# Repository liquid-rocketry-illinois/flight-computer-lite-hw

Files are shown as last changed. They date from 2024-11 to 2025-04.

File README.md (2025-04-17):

# Flight Computer Lite "Digital Tripper"
KiCad PCB repository for "Digital Tripper": a flight computer with no physical outputs designed for uncontrolled solid-fuel excursion flights (the first of which is planned for 2024-11), and a precursor for future flight computers that will incorporate actuation or active control or interact with other boards. The data it gathers will be used for verification of flight control and position estimation algorithms, flight vehicle design iteration, building up a strong avionics software backbone, and field-testing our electronic components and designs. Digital Tripper is a square 65mm on edge and fits transversely in a 4-inch-diameter model rocket.

<p align="center">
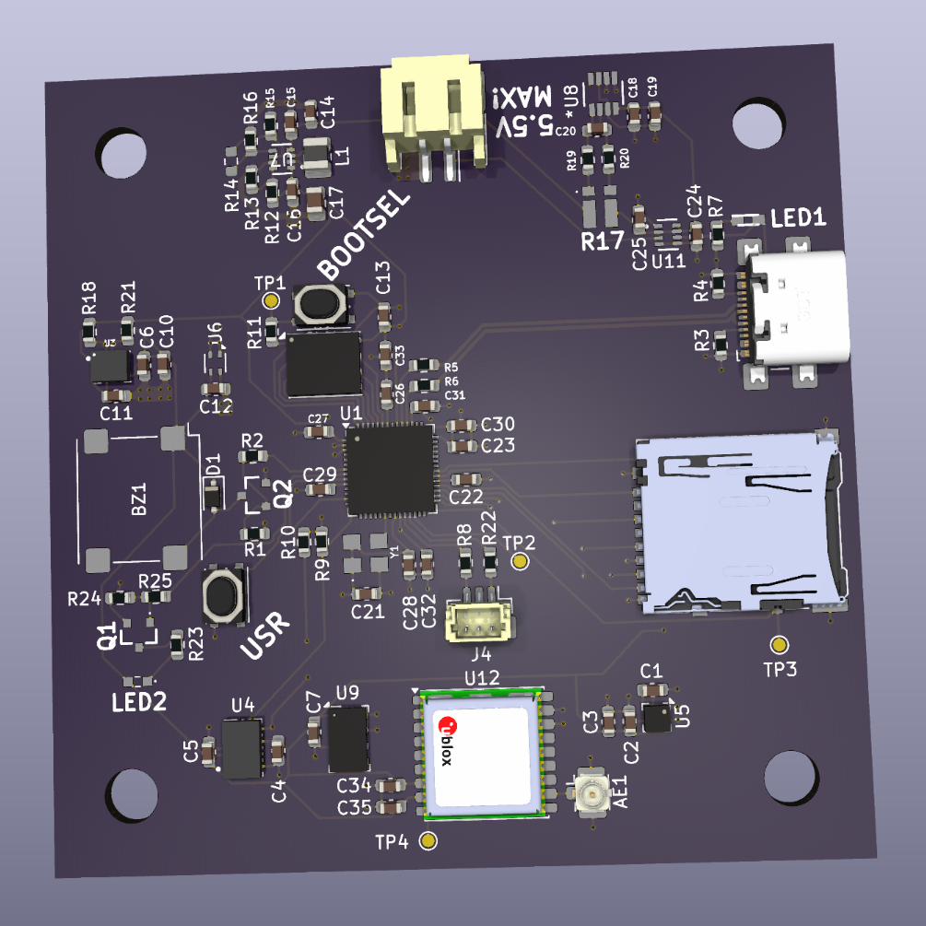
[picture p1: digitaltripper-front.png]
Digital Tripper front render
  
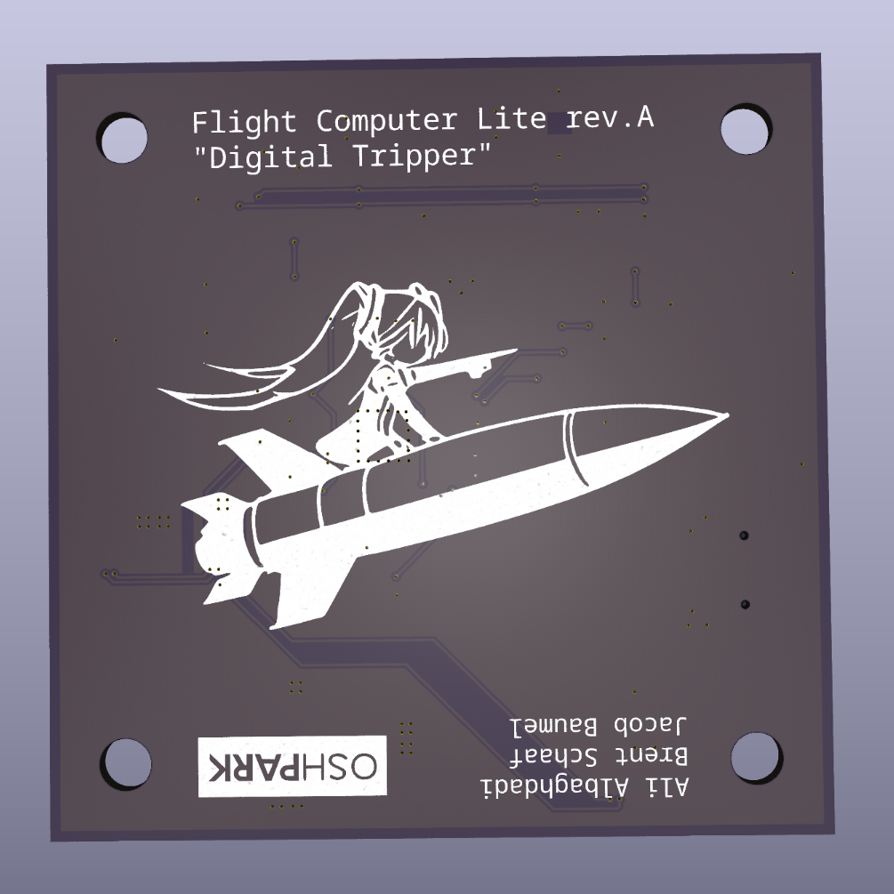
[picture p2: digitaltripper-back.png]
Digital Tripper back render
  
</p>

Ingredients:
* The "brain", a Raspberry Pi Silicon RP2040
* Various digital sensors
    * TDK InvenSense ICM-42688-P high-accuracy 6DoF IMU
    * Bosch BMI088 6DoF IMU for backup and a higher (24 g) acceleration limit
    * STmicroelectronics LIS3MDL 3-axis magnetometer
    * TE Connectivity MS5611 barometer/altimeter
    * Sensirion SHT40 for ambient temperature and humidity
    * u-blox MAX-M10S GNSS receiver with u.FL antenna
* A push-push microSD card slot for vibration-resistant datalogging
* A piezoelectric buzzer to provide audial status information before launch and after landing
* a USB-C port for programming and serial communication with the RP2040
* A JST-PH battery connector
* Power monitor IC to characterize necessary battery size
* A 3.3V-output switching DC-DC converter

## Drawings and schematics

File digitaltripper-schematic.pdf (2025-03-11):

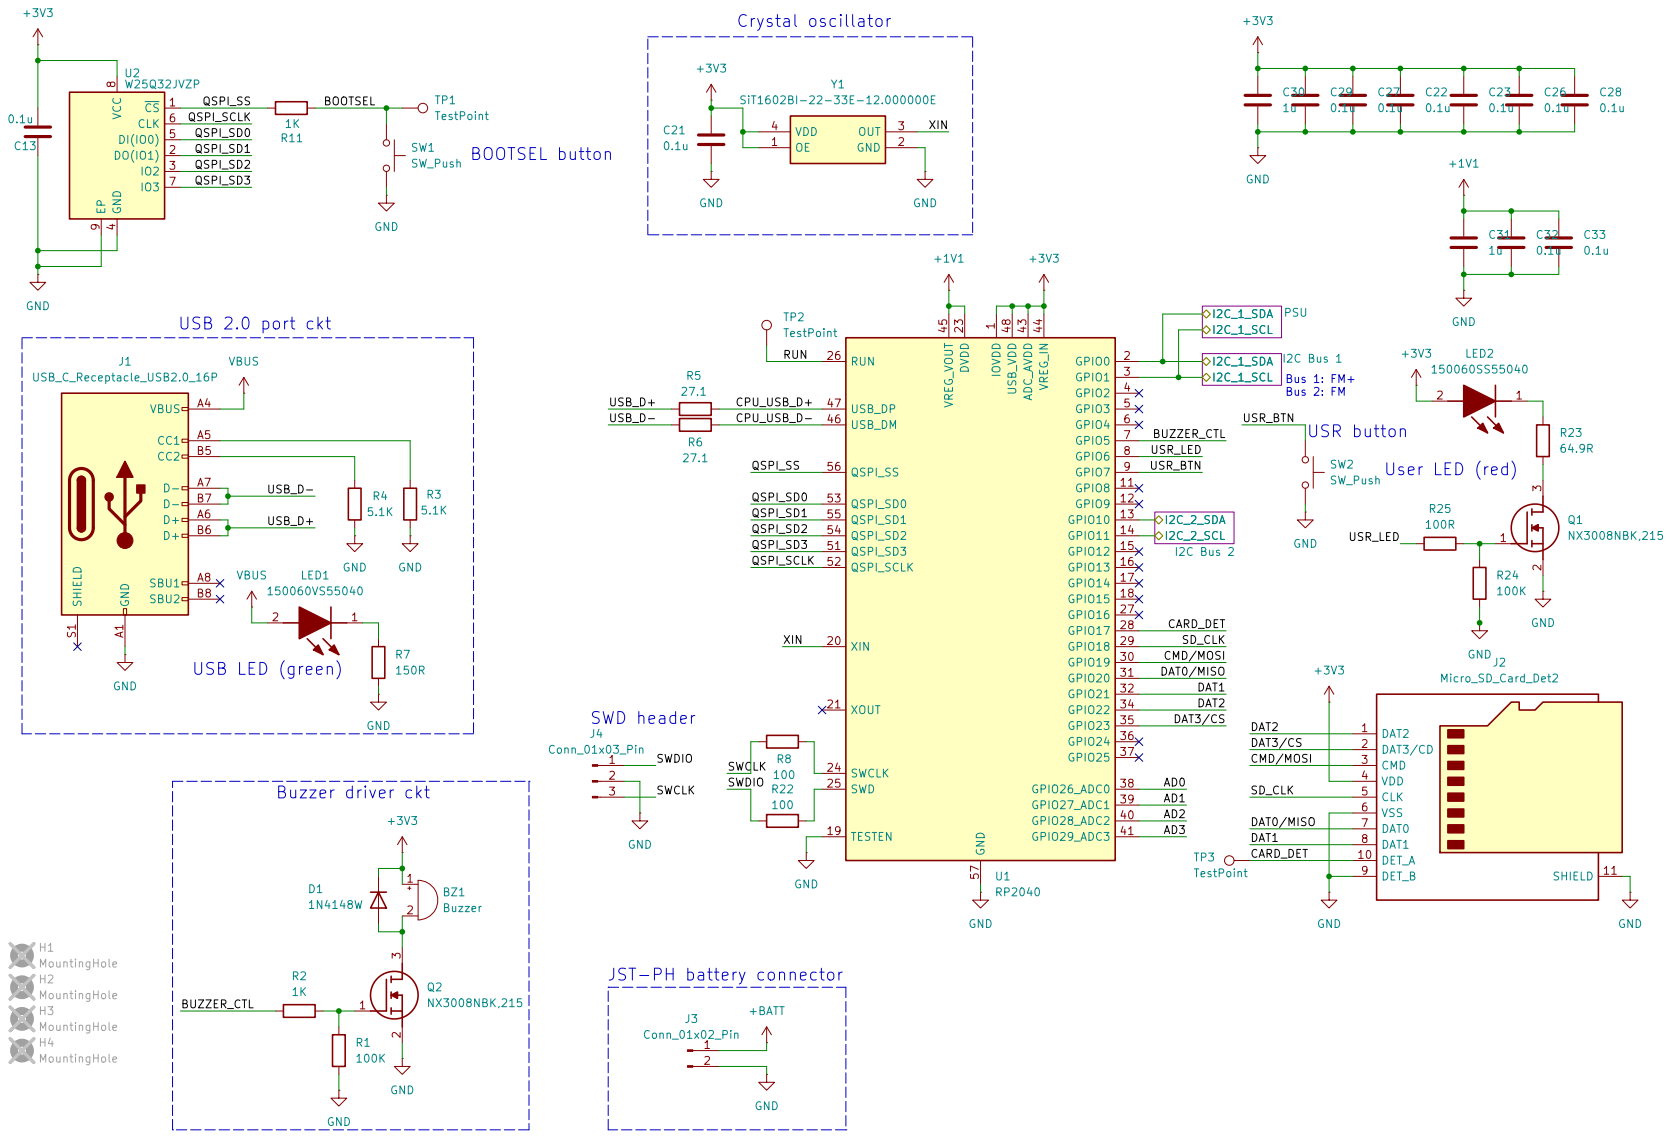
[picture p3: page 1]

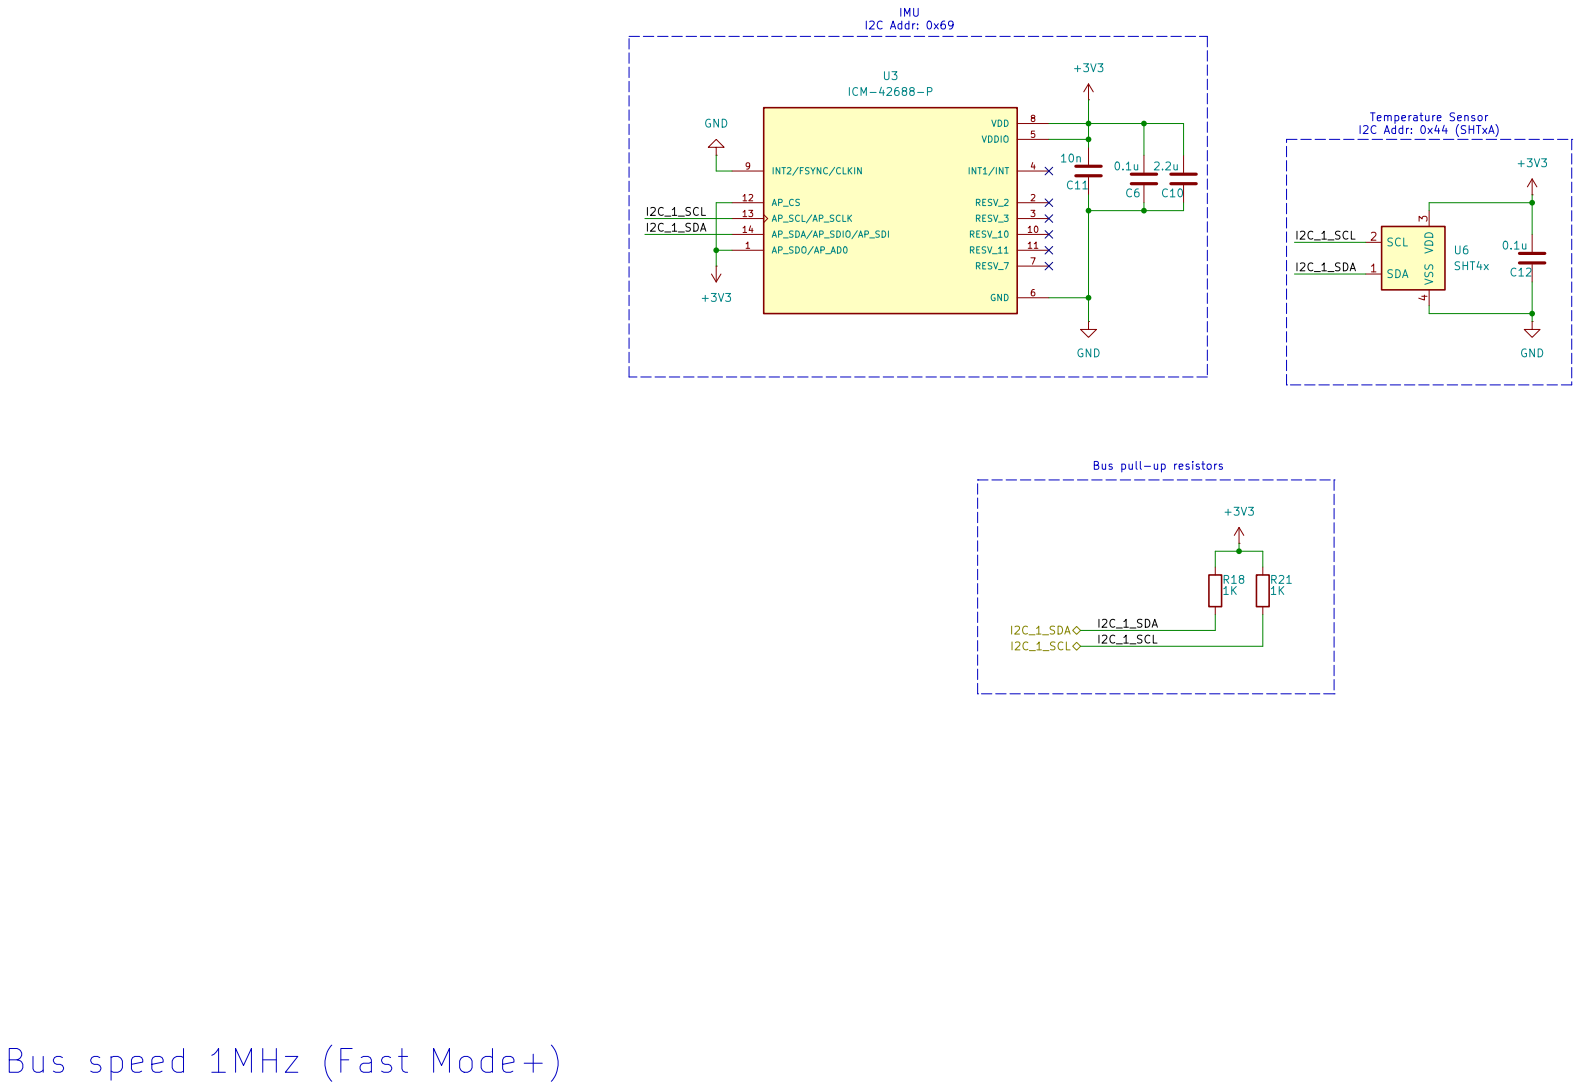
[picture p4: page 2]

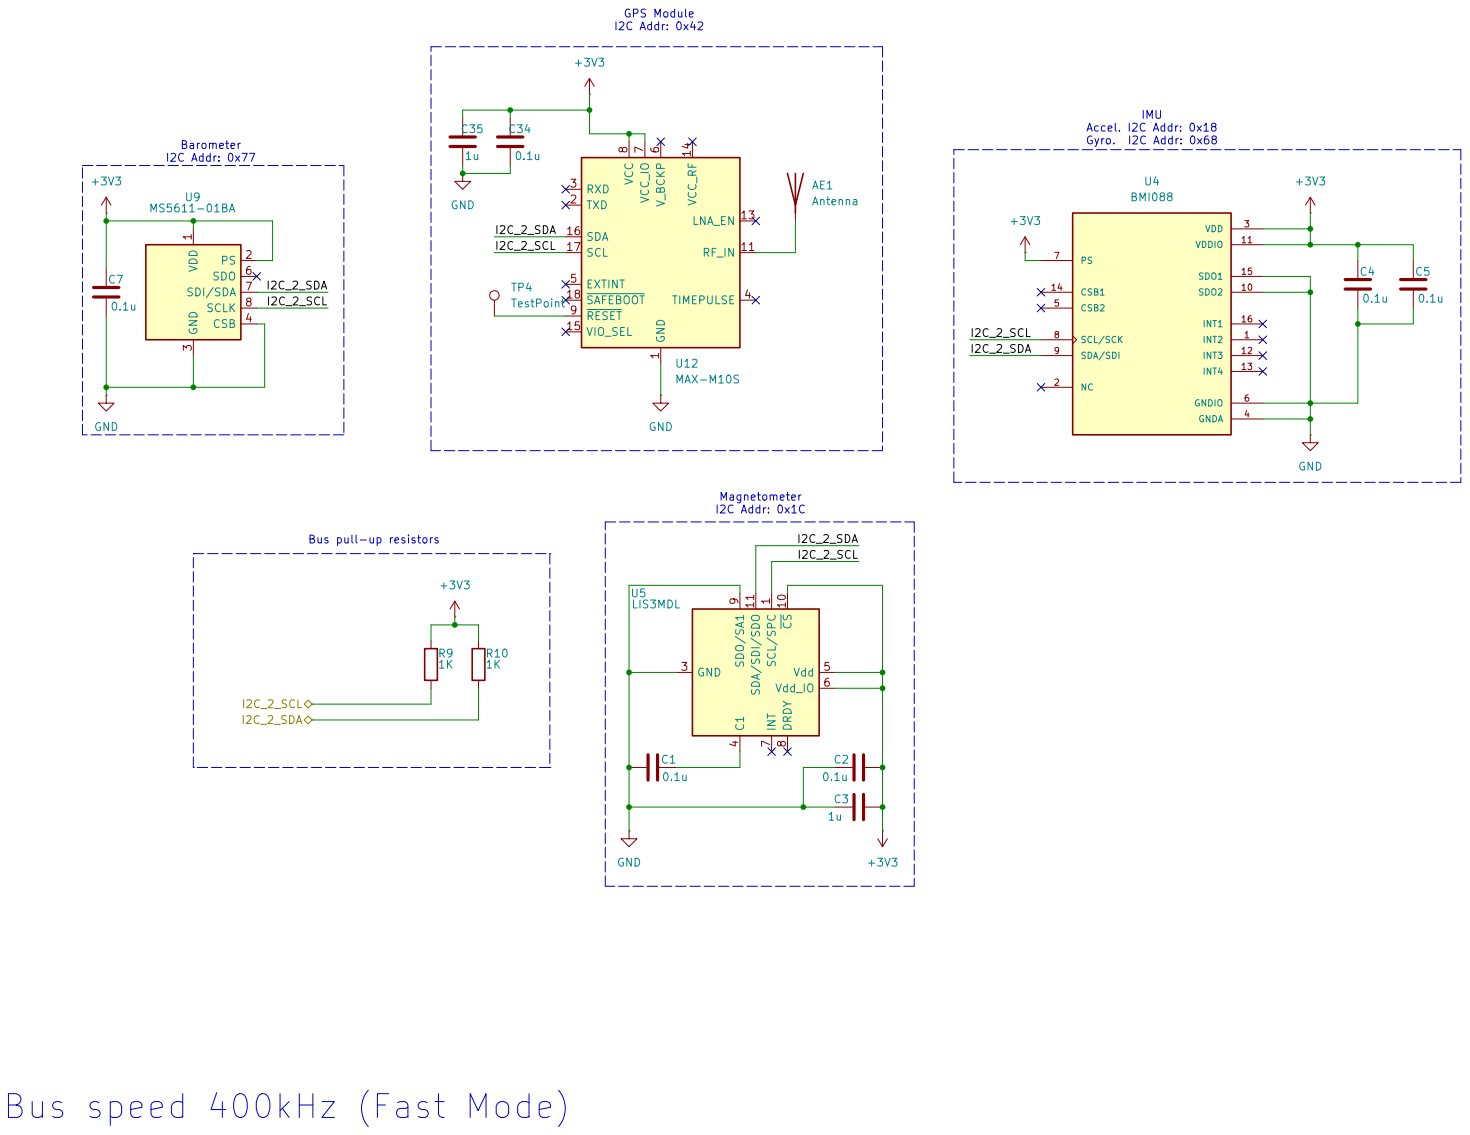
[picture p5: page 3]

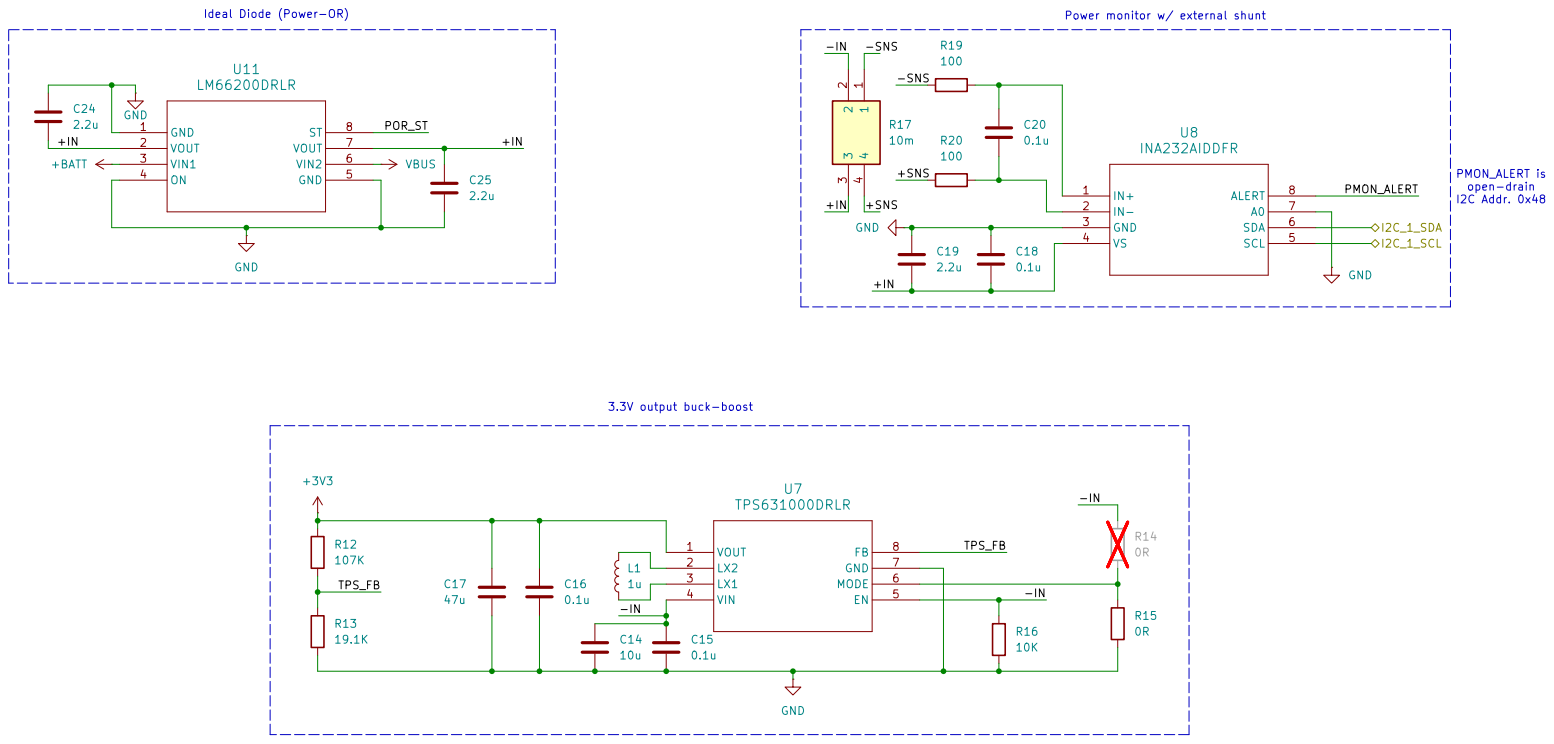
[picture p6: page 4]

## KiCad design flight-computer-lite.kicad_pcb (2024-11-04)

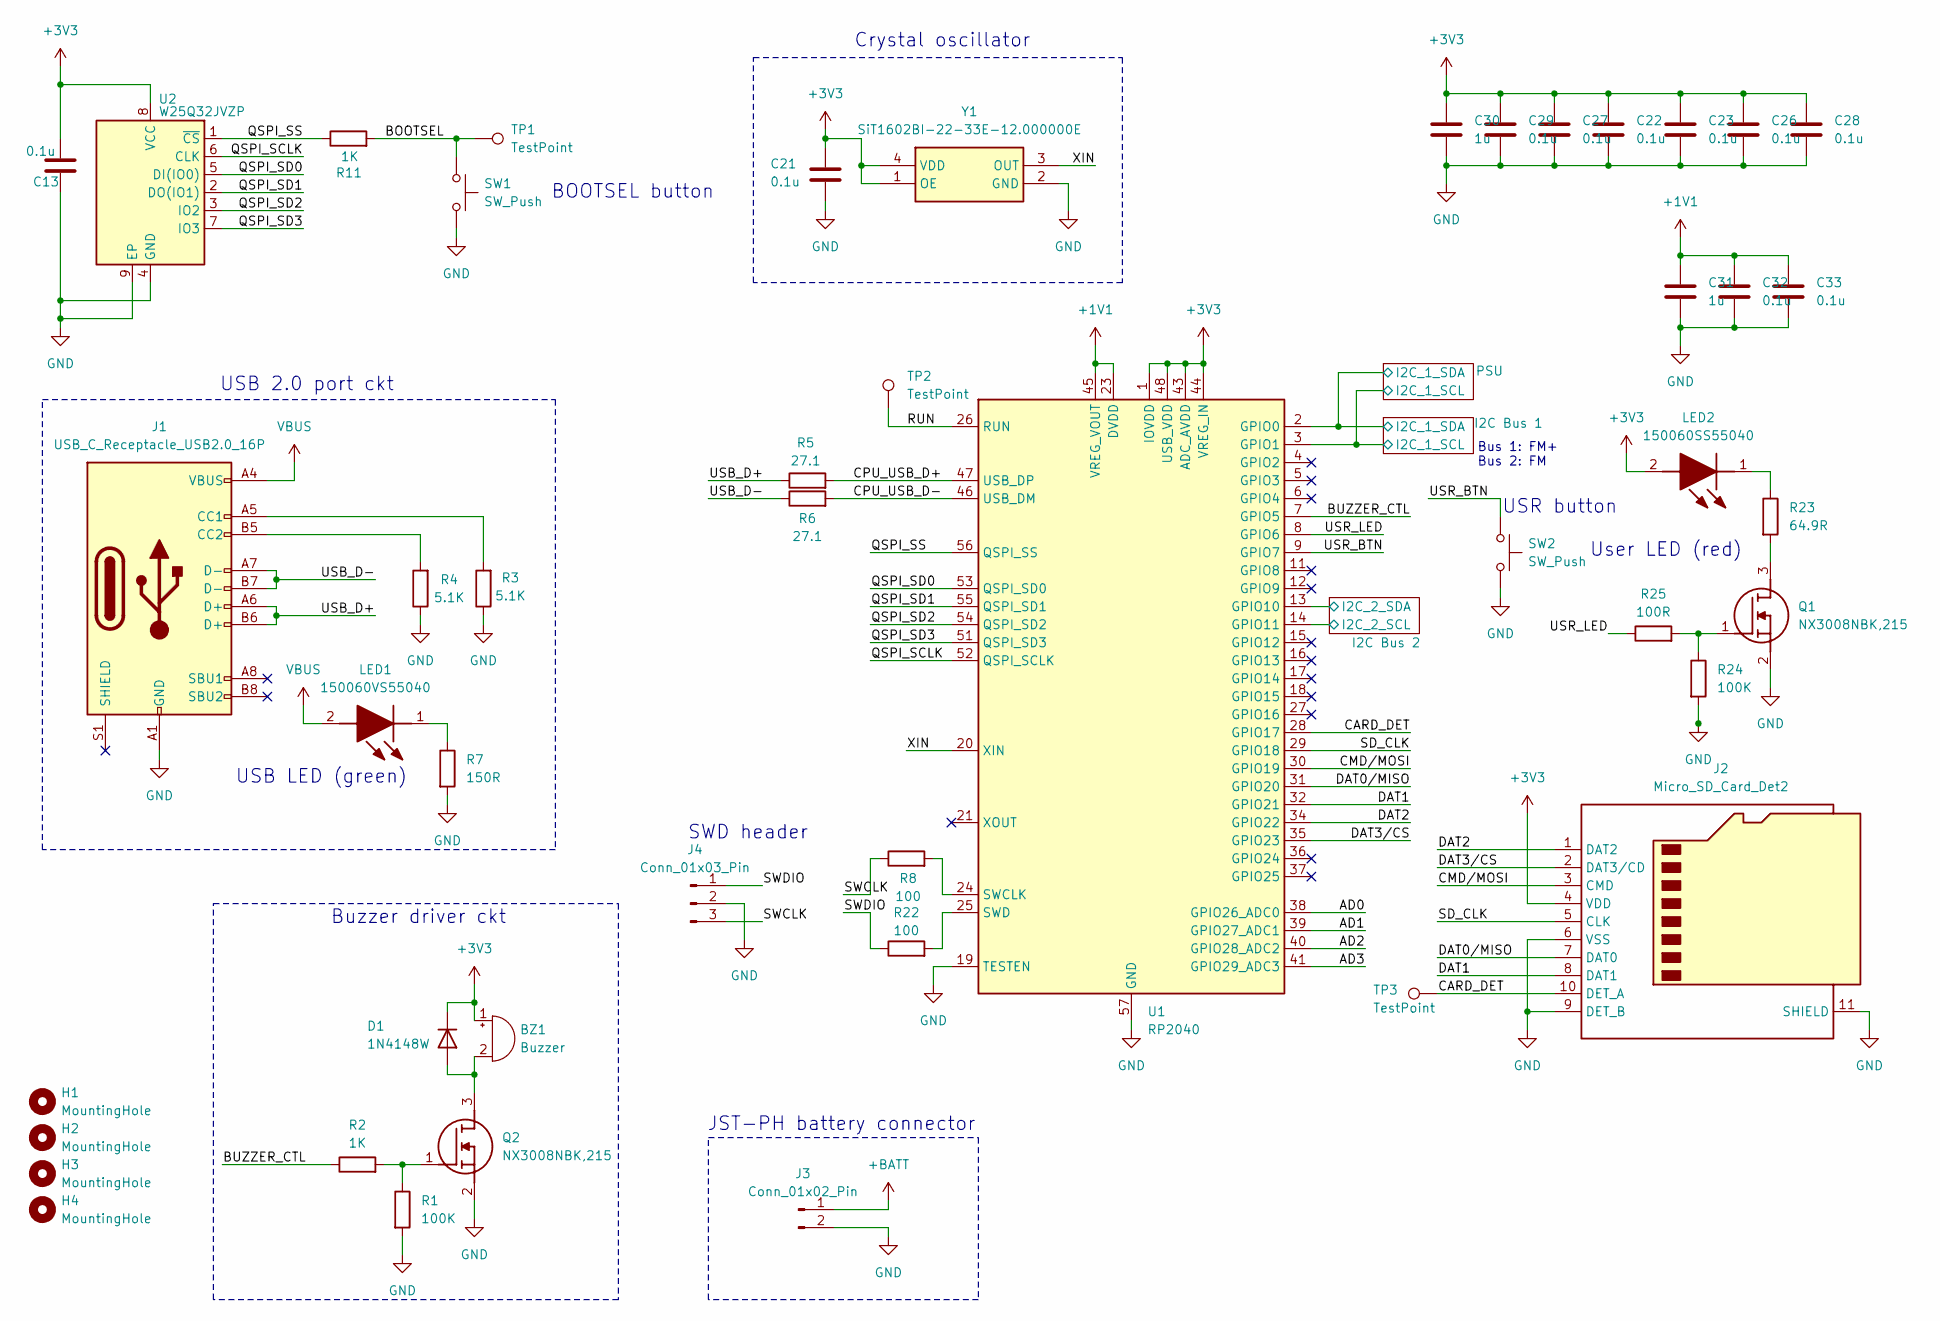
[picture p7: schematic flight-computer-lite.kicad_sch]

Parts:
BZ1: Buzzer; MagneticBuzzer_PUI_SMT-1028-T-2-R
C13, C21, C22, C23, C26, C27, C28, C29, C32, C33: 0.1u; C_0603_1608Metric
C30, C31: 1u; C_0603_1608Metric
D1: 1N4148W; D_SOD-323F
H1, H2, H3, H4: MountingHole; MountingHole_4.3mm_M4
J1: USB_C_Receptacle_USB2.0_16P; USB_C_Receptacle_GCT_USB4110
J2: Micro_SD_Card_Det2; microSD_HC_Hirose_DM3AT-SF-PEJM5
J3: Conn_01x02_Pin; JST_PH_S2B-PH-SM4-TB_1x02-1MP_P2.00mm_Horizontal
J4: Conn_01x03_Pin; JST_SH_BM03B-SRSS-TB_1x03-1MP_P1.00mm_Vertical
LED1: 150060VS55040; LEDM168X50N; Mouser Part Number 710-150060VS55040
LED2: 150060SS55040; Mouser Part Number 710-150060SS55040
Q1, Q2: NX3008NBK,215; NX3008NBK215; Mouser Part Number 771-NX3008NBK,215
R1, R24: 100K; R_0603_1608Metric
R2, R11: 1K; R_0603_1608Metric
R3, R4: 5.1K; R_0603_1608Metric
R5, R6: 27.1; R_0603_1608Metric
R7: 150R; R_0603_1608Metric
R8, R22: 100; R_0603_1608Metric
R23: 64.9R; R_0603_1608Metric
R25: 100R; R_0603_1608Metric
SW1, SW2: SW_Push; SW_Push_1P1T_NO_Vertical_Wuerth_434133025816
TP1, TP2, TP3: TestPoint; TestPoint_Pad_D1.0mm
U1: RP2040; QFN-56-1EP_7x7mm_P0.4mm_EP3.2x3.2mm
U2: W25Q32JVZP; WSON-8-1EP_6x5mm_P1.27mm_EP3.4x4.3mm
Y1: SiT1602BI-22-33E-12.000000E; SIT1602BI2233E12000000G; Manufacturer_Part_Number SiT1602BI-22-33E-12.000000E; Mouser Part Number N/A

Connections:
+1V1: C31.1, C32.1, C33.1, U1.23 (DVDD), U1.45 (VREG_VOUT), U1.50 (DVDD)
+3V3: BZ1.1 (+), C13.1, C21.1, C22.1, C23.1, C26.1, C27.1, C28.1, C29.1, C30.1, D1.1 (K), J2.4 (VDD), LED2.2 (A), U1.1 (IOVDD), U1.10 (IOVDD), U1.22 (IOVDD), U1.33 (IOVDD), U1.42 (IOVDD), U1.43 (ADC_AVDD), U1.44 (VREG_IN), U1.48 (USB_VDD), U1.49 (IOVDD), U2.8 (VCC), Y1.1 (OE), Y1.4 (VDD); also elsewhere on the board
+BATT: J3.1; also elsewhere on the board
/AD0: U1.38 (GPIO26_ADC0)
/AD1: U1.39 (GPIO27_ADC1)
/AD2: U1.40 (GPIO28_ADC2)
/AD3: U1.41 (GPIO29_ADC3)
/BOOTSEL: R11.2, SW1.1, TP1.1
/BUZZER_CTL: R2.1, U1.7 (GPIO5)
/CARD_DET: J2.10 (DET_A), TP3.1, U1.28 (GPIO17)
/CMD/MOSI: J2.3 (CMD), U1.30 (GPIO19)
/CPU_USB_D+: R5.2, U1.47 (USB_DP)
/CPU_USB_D-: R6.2, U1.46 (USB_DM)
/DAT0/MISO: J2.7 (DAT0), U1.31 (GPIO20)
/DAT1: J2.8 (DAT1), U1.32 (GPIO21)
/DAT2: J2.1 (DAT2), U1.34 (GPIO22)
/DAT3/CS: J2.2 (DAT3/CD), U1.35 (GPIO23)
/I2C Bus 1/I2C_1_SCL: U1.3 (GPIO1); also elsewhere on the board
/I2C Bus 1/I2C_1_SDA: U1.2 (GPIO0); also elsewhere on the board
/I2C Bus 2/I2C_2_SCL: U1.14 (GPIO11); also elsewhere on the board
/I2C Bus 2/I2C_2_SDA: U1.13 (GPIO10); also elsewhere on the board
/QSPI_SCLK: U1.52 (QSPI_SCLK), U2.6 (CLK)
/QSPI_SD0: U1.53 (QSPI_SD0), U2.5 (DI(IO0))
/QSPI_SD1: U1.55 (QSPI_SD1), U2.2 (DO(IO1))
/QSPI_SD2: U1.54 (QSPI_SD2), U2.3 (IO2)
/QSPI_SD3: U1.51 (QSPI_SD3), U2.7 (IO3)
/QSPI_SS: R11.1, U1.56 (QSPI_SS), U2.1 (~CS)
/RUN: TP2.1, U1.26 (RUN)
/SD_CLK: J2.5 (CLK), U1.29 (GPIO18)
/SWCLK: J4.3, R8.1
/SWDIO: J4.1, R22.1
/USB_D+: J1.A6 (D+), J1.B6 (D+), R5.1
/USB_D-: J1.A7 (D-), J1.B7 (D-), R6.1
/USR_BTN: SW2.1, U1.9 (GPIO7)
/USR_LED: R25.1, U1.8 (GPIO6)
/XIN: U1.20 (XIN), Y1.3 (OUT)
GND: C13.2, C21.2, C22.2, C23.2, C26.2, C27.2, C28.2, C29.2, C30.2, C31.2, C32.2, C33.2, J1.A1 (GND), J1.A12 (GND), J1.B1 (GND), J1.B12 (GND), J2.6 (VSS), J2.9 (DET_B), J2.11 (SHIELD), J3.2, J4.2, J4.MP, Q1.2 (S), Q2.2 (S), R1.2, R3.1, R4.1, R7.2, R24.2, SW1.2, SW2.2, U1.19 (TESTEN), U1.57 (GND), U2.4 (GND), U2.9 (EP), Y1.2 (GND); also elsewhere on the board
unnamed: BZ1.2 (-), D1.2 (A), Q2.3 (D)
unnamed: J1.A5 (CC1), R3.2
unnamed: J1.B5 (CC2), R4.2
unnamed: LED1.1 (K), R7.1
unnamed: LED2.1 (K), R23.1
unnamed: Q1.3 (D), R23.2
unnamed: Q1.1 (G), R24.1, R25.2
unnamed: Q2.1 (G), R1.1, R2.2
unnamed: R8.2, U1.24 (SWCLK)
unnamed: R22.2, U1.25 (SWD)
VBUS: J1.A4 (VBUS), J1.A9 (VBUS), J1.B4 (VBUS), J1.B9 (VBUS), LED1.2 (A); also elsewhere on the board

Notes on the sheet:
Bus 1: FM+ Bus 2: FM
Buzzer driver ckt
JST-PH battery connector
BOOTSEL button
User LED (red)
SWD header
USB LED (green)
USR button
Crystal oscillator
USB 2.0 port ckt

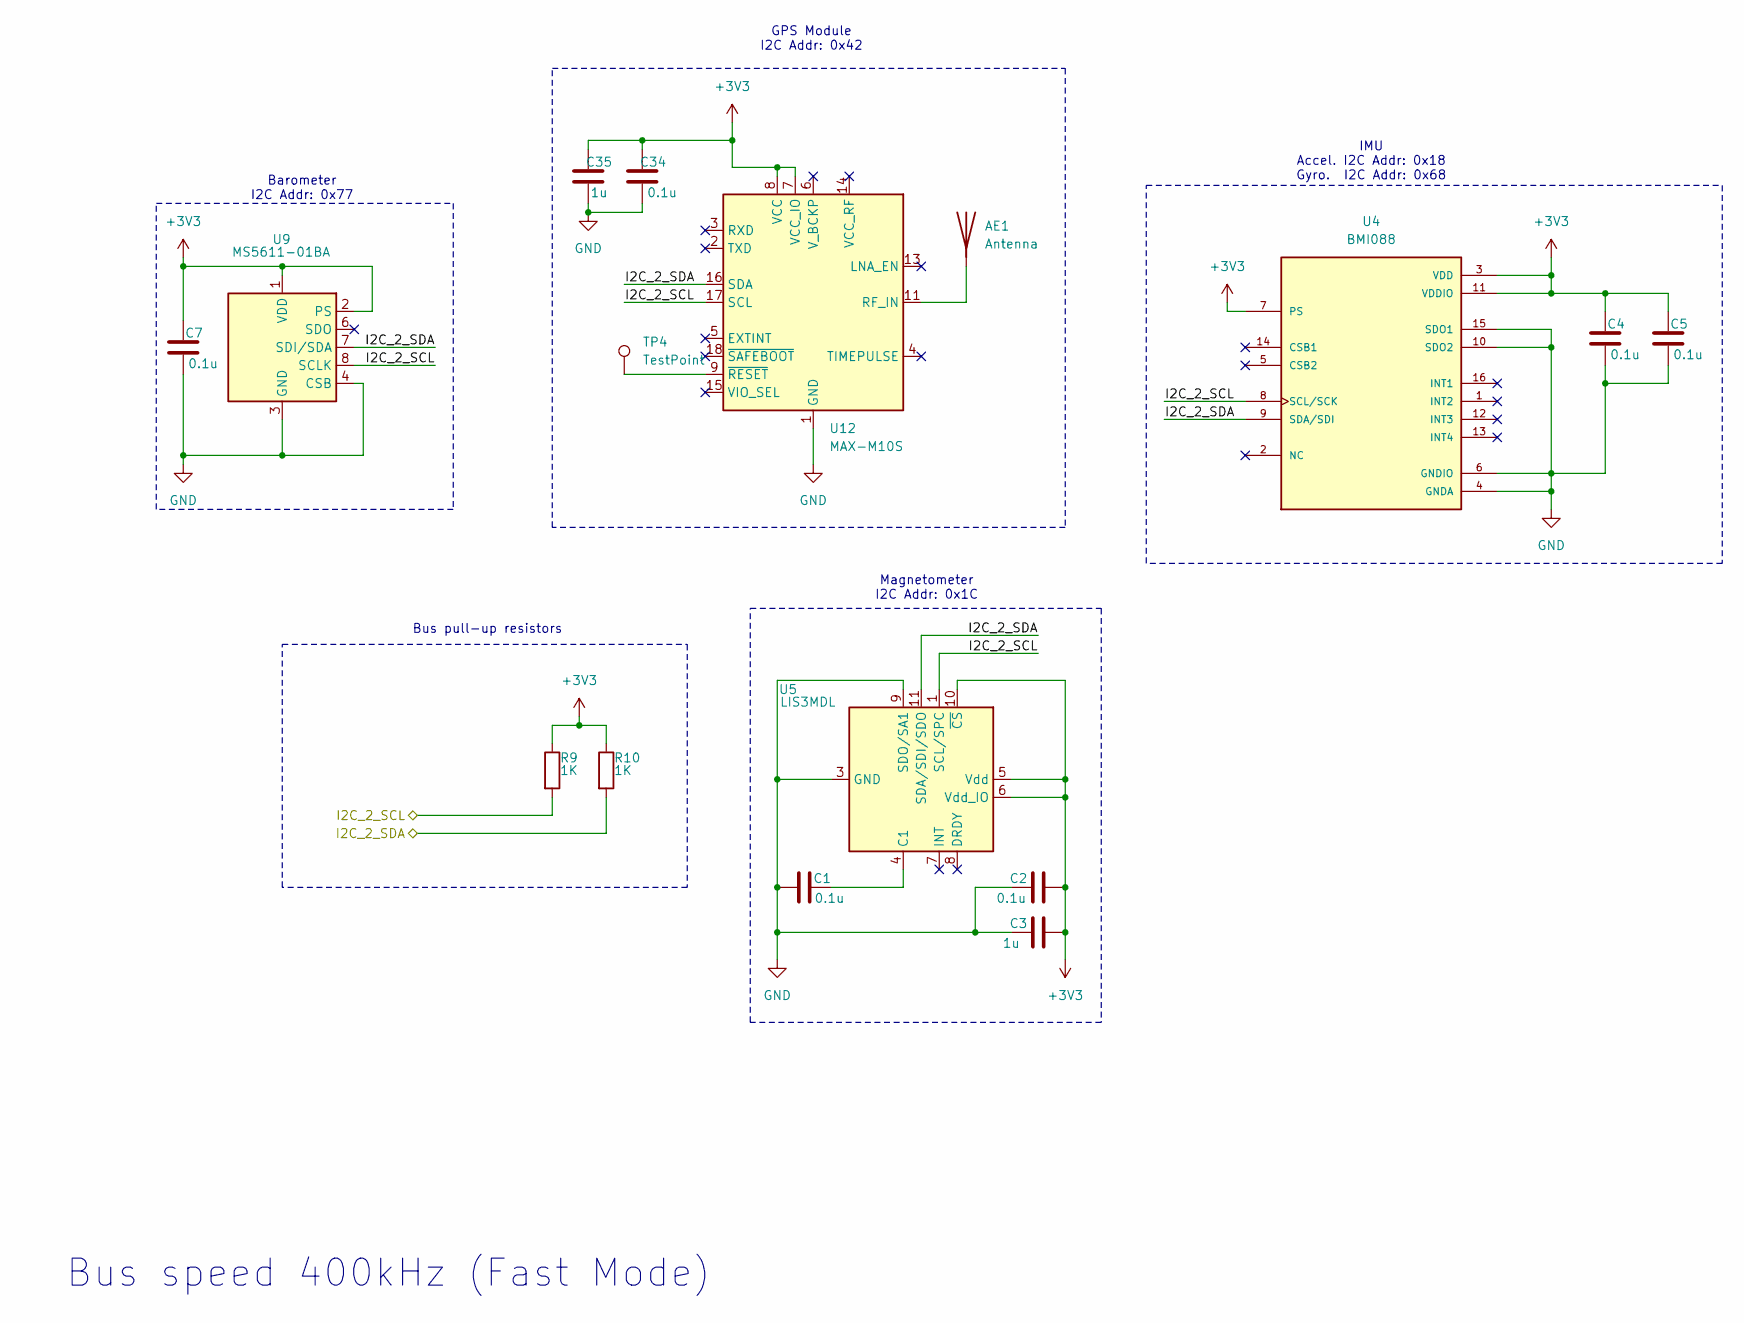
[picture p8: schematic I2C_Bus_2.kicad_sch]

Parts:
AE1: Antenna; U.FL_Hirose_U.FL-R-SMT-1_Vertical
C1, C2, C4, C5, C7, C34: 0.1u; C_0603_1608Metric
C3, C35: 1u; C_0603_1608Metric
R9, R10: 1K; R_0603_1608Metric
TP4: TestPoint; TestPoint_Pad_D1.0mm
U4: BMI088; PQFN50P450X300X100-16N
U5: LIS3MDL; LGA-12_2x2mm_P0.5mm
U9: MS5611-01BA; LGA-8_3x5mm_P1.25mm
U12: MAX-M10S; ublox_MAX

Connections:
+3V3: C2.2, C3.2, C4.2, C5.2, C7.2, C34.2, C35.2, R9.1, R10.1, U4.3 (VDD), U4.7 (PS), U4.11 (VDDIO), U5.5 (Vdd), U5.6 (Vdd_IO), U5.10 (~CS), U9.1 (VDD), U9.2 (PS), U12.7 (VCC_IO), U12.8 (VCC); also elsewhere on the board
/I2C Bus 2/I2C_2_SCL: R9.2, U4.8 (SCL/SCK), U5.1 (SCL/SPC), U9.8 (SCLK), U12.17 (SCL); also elsewhere on the board
/I2C Bus 2/I2C_2_SDA: R10.2, U4.9 (SDA/SDI), U5.11 (SDA/SDI/SDO), U9.7 (SDI/SDA), U12.16 (SDA); also elsewhere on the board
GND: AE1.2, C1.1, C2.1, C3.1, C4.1, C5.1, C7.1, C34.1, C35.1, U4.4 (GNDA), U4.6 (GNDIO), U4.10 (SDO2), U4.15 (SDO1), U5.2 (GND), U5.3 (GND), U5.9 (SDO/SA1), U5.12 (GND), U9.3 (GND), U9.4 (CSB), U9.5 (CSB), U12.1 (GND), U12.10 (GND), U12.12 (GND); also elsewhere on the board
unnamed: AE1.1 (A), U12.11 (RF_IN)
unnamed: C1.2, U5.4 (C1)
unnamed: TP4.1, U12.9 (~RESET)

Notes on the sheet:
Magnetometer I2C Addr: 0x1C
IMU Accel. I2C Addr: 0x18 Gyro. I2C Addr: 0x68
GPS Module I2C Addr: 0x42
Bus pull-up resistors
Bus speed 400kHz (Fast Mode)
Barometer I2C Addr: 0x77

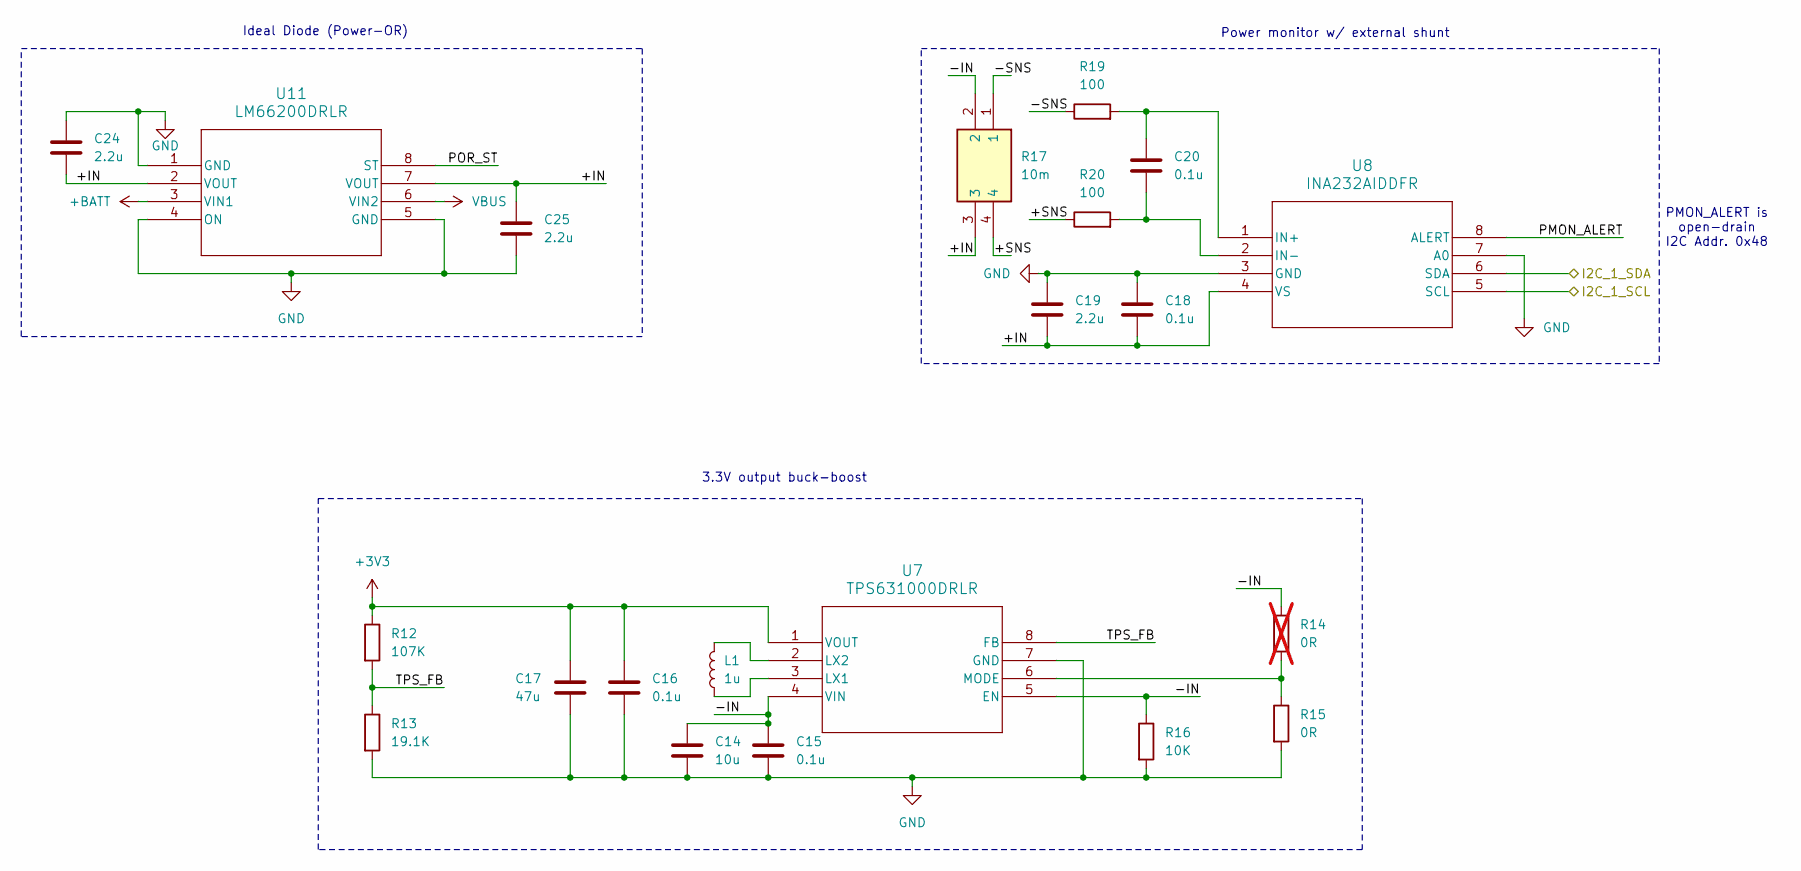
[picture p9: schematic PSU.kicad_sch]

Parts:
C14: 10u; C_0603_1608Metric
C15, C16, C18, C20: 0.1u; C_0603_1608Metric
C17: 47u; C_0805_2012Metric
C19, C24, C25: 2.2u; C_0603_1608Metric
L1: 1u; L_1008_2520Metric
R12: 107K; R_0603_1608Metric
R13: 19.1K; R_0603_1608Metric
R14: 0R; R_0603_1608Metric; not fitted
R15: 0R; R_0603_1608Metric
R16: 10K; R_0603_1608Metric
R17: 10m; L4CA0612L0M50FNR; Manufacturer_Part_Number L4CA0612LR010FNR
R19, R20: 100; R_0603_1608Metric
U7: TPS631000DRLR; TPS631000DRLR_TEX
U8: INA232AIDDFR
U11: LM66200DRLR; LM66200

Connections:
+3V3: C16.1, C17.1, R12.1, U7.1 (VOUT); also elsewhere on the board
+BATT: U11.3 (VIN1); also elsewhere on the board
/I2C Bus 1/I2C_1_SCL: U8.5 (SCL); also elsewhere on the board
/I2C Bus 1/I2C_1_SDA: U8.6 (SDA); also elsewhere on the board
/PSU/+IN: C18.2, C19.2, C24.2, C25.1, R17.3, U8.4 (VS), U11.2 (VOUT), U11.7 (VOUT)
/PSU/+SNS: R17.4, R20.1
/PSU/-IN: C14.1, C15.1, R14.1, R16.1, R17.2, U7.4 (VIN), U7.5 (EN)
/PSU/-SNS: R17.1, R19.1
/PSU/PMON_ALERT: U8.8 (ALERT)
/PSU/POR_ST: U11.8 (ST)
/PSU/TPS_FB: R12.2, R13.1, U7.8 (FB)
GND: C14.2, C15.2, C16.2, C17.2, C18.1, C19.1, C24.1, C25.2, R13.2, R15.2, R16.2, U7.7 (GND), U8.3 (GND), U8.7 (A0), U11.1 (GND), U11.4 (ON), U11.5 (GND); also elsewhere on the board
unnamed: L1.1, U7.3 (LX1)
unnamed: L1.2, U7.2 (LX2)
unnamed: R14.2, R15.1, U7.6 (MODE)
unnamed: C20.1, R19.2, U8.1 (IN+)
unnamed: C20.2, R20.2, U8.2 (IN-)
VBUS: U11.6 (VIN2); also elsewhere on the board

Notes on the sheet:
Power monitor w/ external shunt
PMON_ALERT is open-drain I2C Addr. 0x48
3.3V output buck-boost
Ideal Diode (Power-OR)

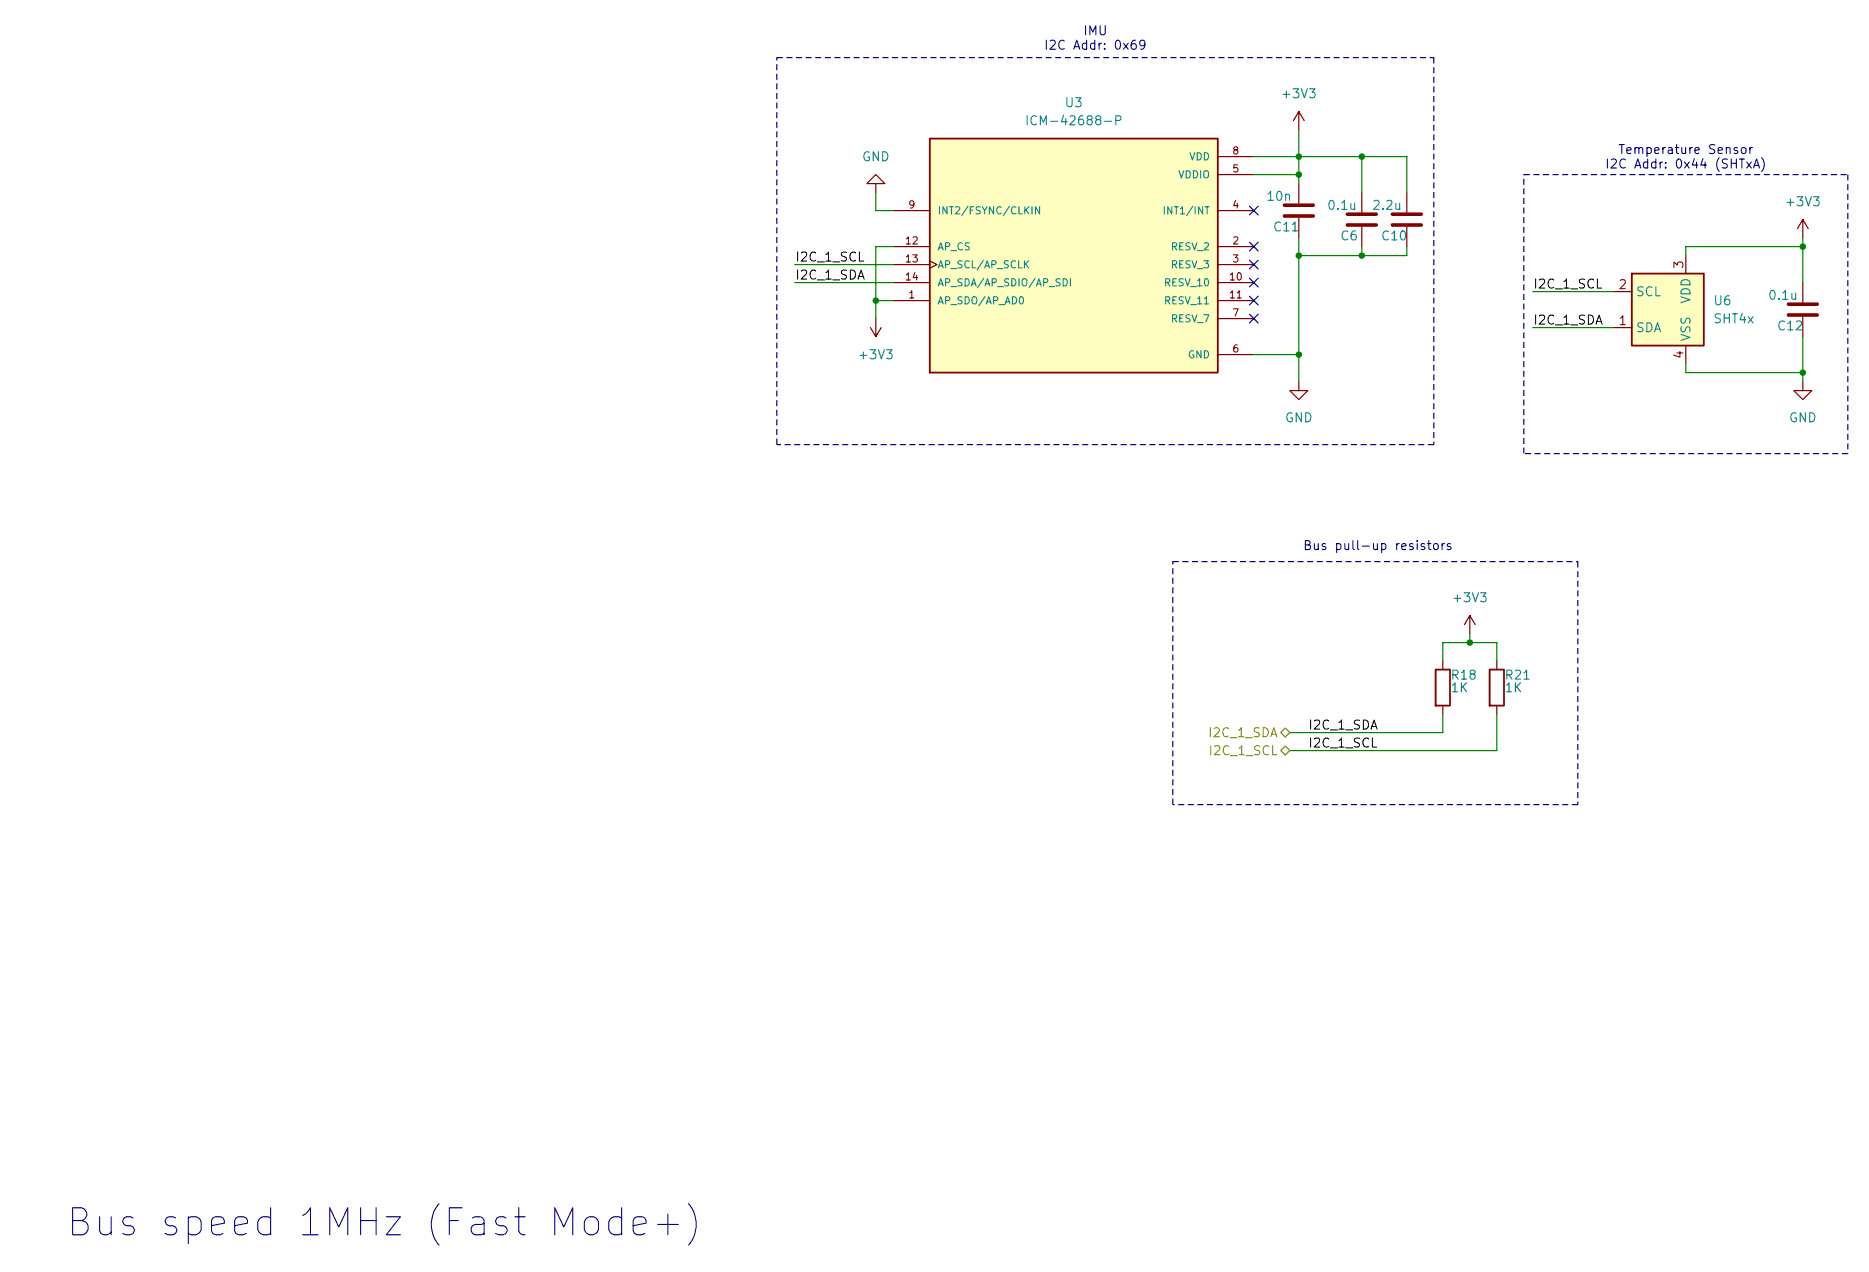
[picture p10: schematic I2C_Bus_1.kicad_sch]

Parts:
C6, C12: 0.1u; C_0603_1608Metric
C10: 2.2u; C_0603_1608Metric
C11: 10n; C_0603_1608Metric
R18, R21: 1K; R_0603_1608Metric
U3: ICM-42688-P; PQFN50P300X250X97-14N; PARTREV 1.2
U6: SHT4x; Sensirion_DFN-4_1.5x1.5mm_P0.8mm_SHT4x_NoCentralPad

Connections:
+3V3: C6.2, C10.2, C11.2, C12.2, R18.1, R21.1, U3.1 (AP_SDO/AP_AD0), U3.5 (VDDIO), U3.8 (VDD), U3.12 (AP_CS), U6.3 (VDD); also elsewhere on the board
/I2C Bus 1/I2C_1_SCL: R21.2, U3.13 (AP_SCL/AP_SCLK), U6.2 (SCL); also elsewhere on the board
/I2C Bus 1/I2C_1_SDA: R18.2, U3.14 (AP_SDA/AP_SDIO/AP_SDI), U6.1 (SDA); also elsewhere on the board
GND: C6.1, C10.1, C11.1, C12.1, U3.6 (GND), U3.9 (INT2/FSYNC/CLKIN), U6.4 (VSS); also elsewhere on the board

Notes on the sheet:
Temperature Sensor I2C Addr: 0x44 (SHTxA)
IMU I2C Addr: 0x69
Bus speed 1MHz (Fast Mode+)
Bus pull-up resistors

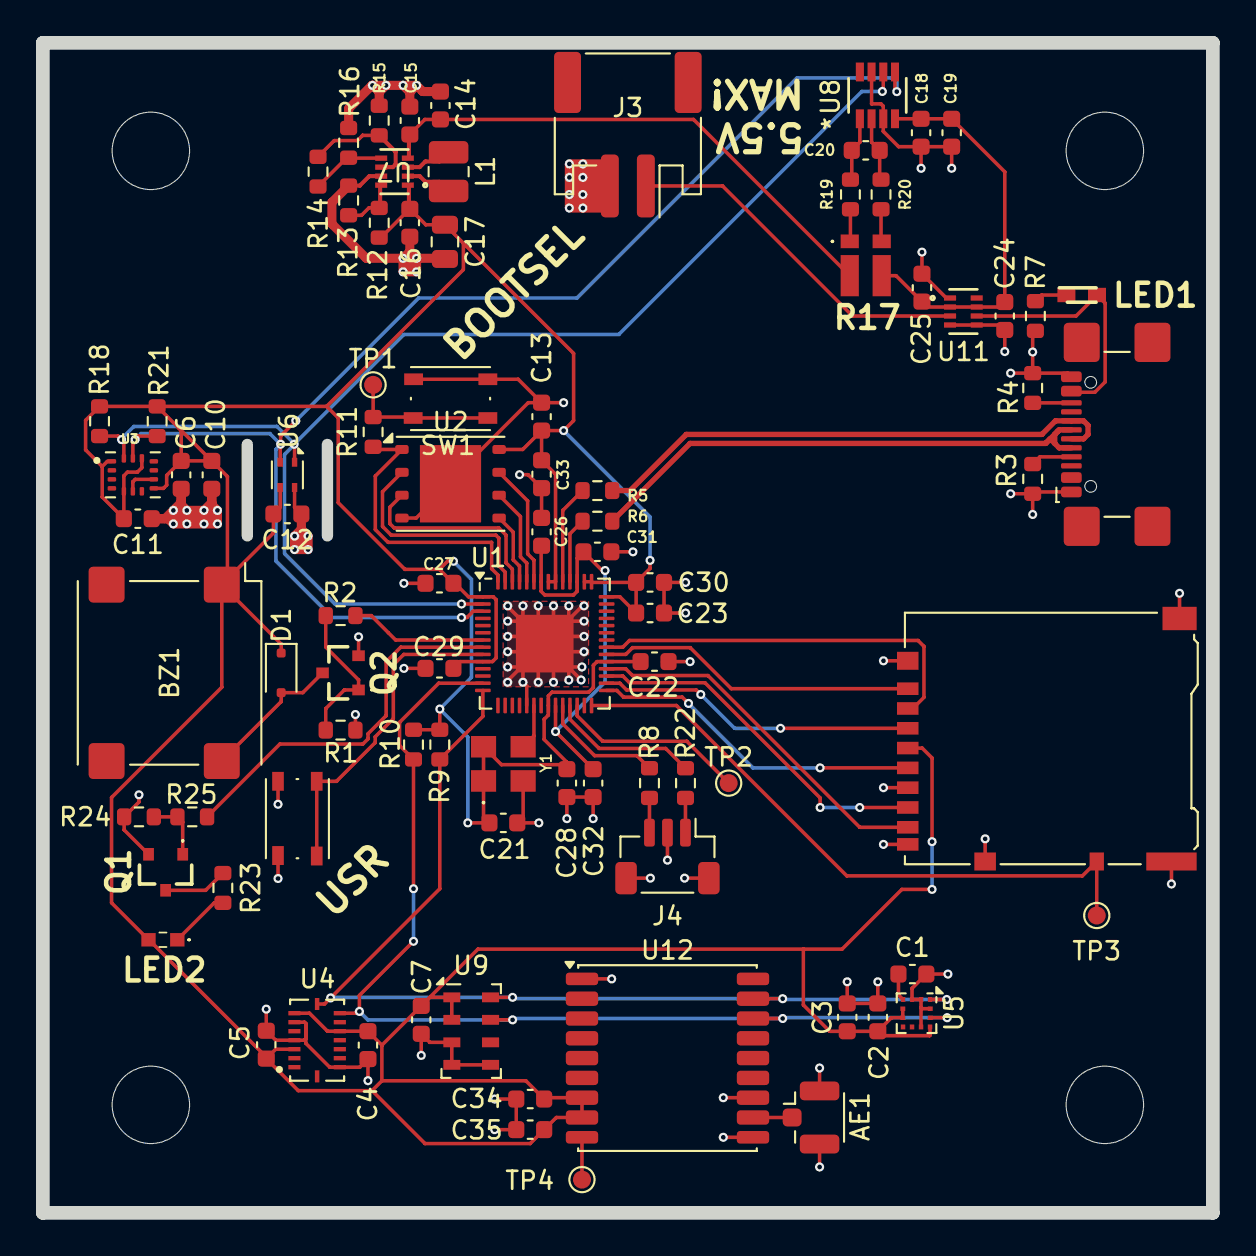
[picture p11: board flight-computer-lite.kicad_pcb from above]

Board: 2 copper layers, 65.0 x 65.0 mm, 92 parts (0 on the bottom side), 57 nets.

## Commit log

2024-09-10 Initial commit of KiCad files
    [flight-computer-lite.kicad_pcb, flight-computer-lite.kicad_sch]
2024-09-10 Added mounting holes
    [flight-computer-lite.kicad_pcb, flight-computer-lite.kicad_sch]
2024-09-10 Changed board surface finish, added GPS
    [flight-computer-lite.kicad_pcb, flight-computer-lite.kicad_sch]
2024-09-11 replaced nrnd BME680 with HDC2080
    [flight-computer-lite.kicad_pcb, flight-computer-lite.kicad_sch]
2024-09-12 Changed buzzer partno
    [flight-computer-lite.kicad_pcb, flight-computer-lite.kicad_sch]
2024-09-22 Created LRI_partlib
    Created a local part library for the project (that can be reused on others in the future).
    Added the ICM-42688-P and BMI088 IMUs to it.
    Added them to the PCB and reorganized some things.
    [flight-computer-lite.kicad_pcb, flight-computer-lite.kicad_sch]
2024-09-23 Added battery, updated USB
    [flight-computer-lite.kicad_pcb, flight-computer-lite.kicad_sch]
2024-09-24 Added I2C Devices
    [I2C_Bus_1.kicad_sch, I2C_Bus_2.kicad_sch, flight-computer-lite.kicad_sch]
2024-09-24 Changed Battery Connector Footprint
    [flight-computer-lite.kicad_sch]
2024-09-24 Wired flash
    [flight-computer-lite.kicad_sch]
2024-09-30 Added buck-boost
    [I2C_Bus_1.kicad_sch, I2C_Bus_2.kicad_sch, PSU.kicad_sch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]
2024-10-02 Finished PSU
    [PSU.kicad_sch, flight-computer-lite.kicad_sch]
2024-10-07 Added buttons, LEDs, TPs, and Miku
    [I2C_Bus_1.kicad_sch, I2C_Bus_2.kicad_sch, PSU.kicad_sch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]
2024-10-07 Added more decoupling caps
    [flight-computer-lite.kicad_pcb, flight-computer-lite.kicad_sch]
2024-10-07 Added more 3d models and rearranged layout
    [flight-computer-lite.kicad_pcb, flight-computer-lite.kicad_sch]
2024-10-08 Tentatively finished schematic
    [I2C_Bus_2.kicad_sch, PSU.kicad_sch, flight-computer-lite.kicad_sch]
2024-10-08 Added I2C resistor values
    [I2C_Bus_1.kicad_sch, I2C_Bus_2.kicad_sch, PSU.kicad_sch]
2024-10-09 Moved LIS3MDL to FM bus
    [I2C_Bus_1.kicad_sch, I2C_Bus_2.kicad_sch]
2024-10-12 Changed out GPS module
    [I2C_Bus_2.kicad_sch]
2024-10-12 Added 3D model for MAX-M10S and adjusted footprint
    [I2C_Bus_2.kicad_sch]
2024-10-12 Changed FM I2C bus pins
    [flight-computer-lite.kicad_sch]
2024-10-12 oops wrong pins
    [flight-computer-lite.kicad_sch]
2024-10-12 Fixed hierarchy pins in I2C 1 bus schematic
    [I2C_Bus_1.kicad_sch, flight-computer-lite.kicad_sch]
2024-10-12 Adjusted VREG IN/OUT Decoupling capacitor values to match datasheet suggestion
    [flight-computer-lite.kicad_sch]
2024-10-12 Changed USR_LED and USR_BTN pins
    [flight-computer-lite.kicad_sch]
2024-10-12 oops wrong pin again
    [flight-computer-lite.kicad_sch]
2024-10-14 WIP layout/route
    [I2C_Bus_1.kicad_sch, I2C_Bus_2.kicad_sch, flight-computer-lite.kicad_pcb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]
2024-10-19 Routed PSU
    [I2C_Bus_1.kicad_sch, I2C_Bus_2.kicad_sch, PSU.kicad_sch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]
2024-10-20 Adjusted footprints for LIS3MDL and BMI088
2024-10-21 Adjusted ICM42688 footprint
2024-10-21 Adjusted LM66200 pcb
2024-10-22 major routing update!
    [I2C_Bus_1.kicad_sch, I2C_Bus_2.kicad_sch, PSU.kicad_sch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]
2024-10-22 Moved pin numbers on remaining parts
2024-10-23 Fixed PSU, routed
    [I2C_Bus_1.kicad_sch, I2C_Bus_2.kicad_sch, PSU.kicad_sch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]
2024-10-24 Almost done with routing
    [flight-computer-lite.kicad_pcb]
2024-10-28 Silkscreen finished
    [I2C_Bus_1.kicad_sch, I2C_Bus_2.kicad_sch, PSU.kicad_sch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]
2024-10-29 Fixed slots
    [flight-computer-lite.kicad_pcb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]
2024-10-29 Moved back silkscreen
    [flight-computer-lite.kicad_pcb]
2024-10-30 Design complete (hopefully)
    [flight-computer-lite.kicad_pcb]
2025-03-11 Schematic exported to PDF
